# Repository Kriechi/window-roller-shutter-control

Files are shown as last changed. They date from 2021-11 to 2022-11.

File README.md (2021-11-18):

# Window Roller Shutter Control 3-gang with ESP8266

This project contains a 3-gang electric/motorized window roller shutter control
based on an ESP8266. The following resources are included:

* Full schematics and PCB designs
  * in KiCAD 5 with all footprints
  * generated Gerber files ready to send to PCB manufacturer
  * exported as PDF file
* Microcontroller ESP8266 firmware source code
  * with WiFi connectivity and remote over-the-air update
  * for control via MQTT and a web interface
* 3D-printable enclosure
  * in 3MF and STL file formats

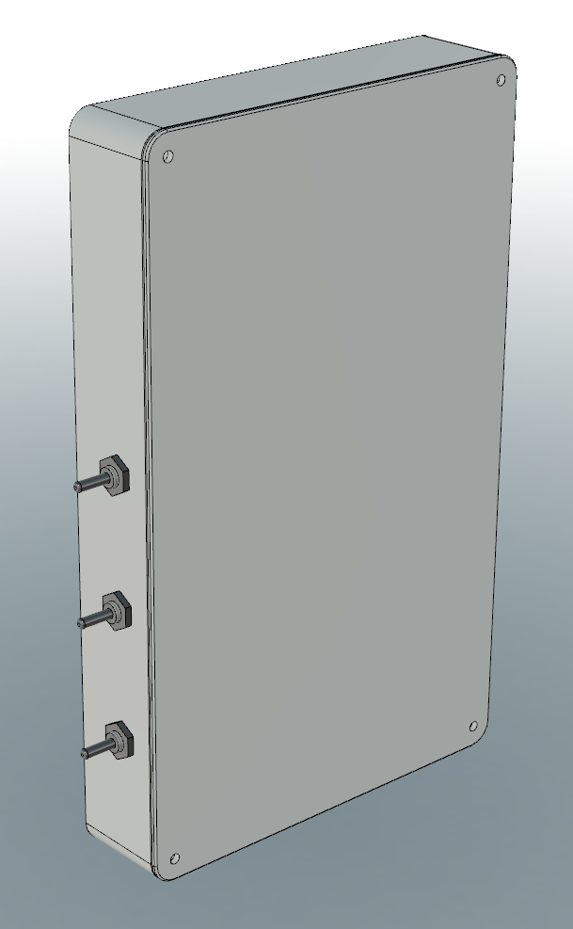
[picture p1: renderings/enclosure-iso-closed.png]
enclosure-iso-closed


## Hardware

This projects was designed to control 3 independent electric roller shutter
motors, each with a hot (live) and two switched directional wires (L1 for "up"
and L2 for "down"). Existing manual switches need to be removed and the motor
cables are wired to screw terminals on the PCB. Two relays per roller shutter
control the direction: up or down. The circuit and the relay type ensure that
only one direction is possible at a time. The relays open before closing
(break-before-make), and both relays are arranged "in series" to control the
motor direction.

The PCB and enclosure are designed to fit around an existing 3-gang 60mm switch
box. Any common 3-gang switch plate for this size can be replaced by the PCB and
enclosure, given that each switch box is 72mm apart from its neighbor switch
box. The enclosure mounts flush against the wall and is secured by multiple
screws into the switch box behind it.

Since not every roller shutter provides a neutral (return) wire, an external
5-24VDC power supply (wall plug) is used to power the ESP8266 and relays on PCB.
This securely separates low-voltage from high-voltage, also see separation slots
on the PCB. Multiple footprints are on the PCB to feed in DC low-voltage.

Momentary toggle switches can be added to manually control the roller shutters,
independent of the ESP8266 or automation. The enclosure is designed for 6mm
toggle switches. They control the relays low-voltage side and override signals
from the ESP8266.

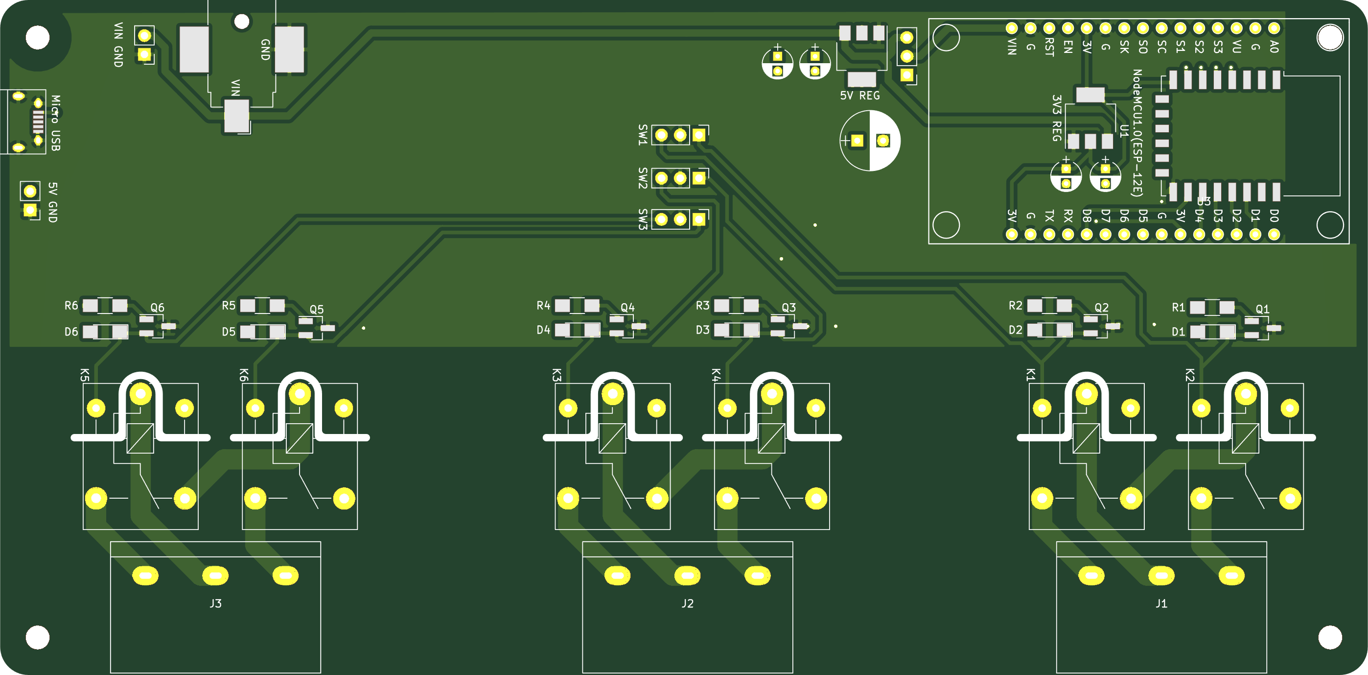
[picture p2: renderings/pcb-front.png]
pcb-front

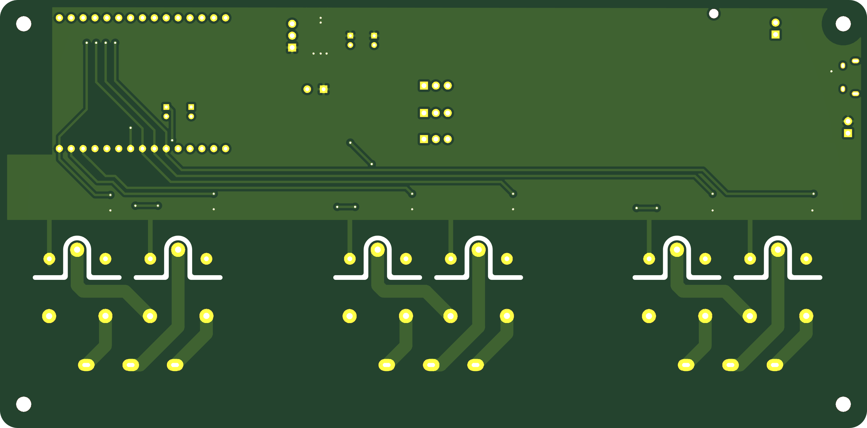
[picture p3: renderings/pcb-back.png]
pcb-back


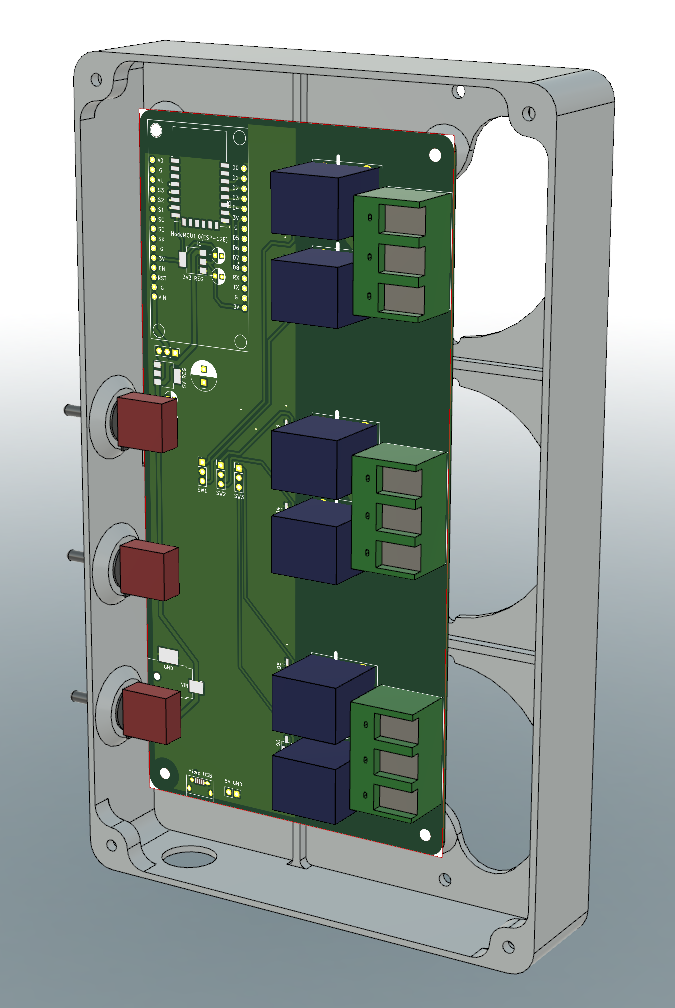
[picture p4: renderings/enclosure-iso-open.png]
enclosure-iso-open


### Bill of Material

For the PCB assembly:

* 1x NodeMCU module for ESP8266, or ESP-12E module (requires additional components)
* 3x HB-9500 3P screw terminal, 9.5mm pitch
* 6x SRD-05VDC-SL-C relay, 5VDC control, opening before closing, 10A@250VAC
* 6x NPN transistor, footprint SOT-23, 2N3904 or similar
* 6x 220 Ohm resistor, footprint 1206
* 6x flyback diode, footprint 1206, 1N4001 or similar
* 3x MTS-123 On-Off-On toggle switch
* 1x 5V DC-DC voltage regulator, footprint SOT-223-3, AMS1117-50 or similar
* 1x 3.3V DC-DC voltage regulator if ESP-12E is used, footprint SOT-223-3, AMS1117-33 or similar
* 1x suitable power supply for 5VDC, at least 10W
* optional: capacitors as needed per voltage rail

For the enclosure and mounting:

* 8x M3 nut
* 4x M3x12 bolts
* 2x 3.2mm switch box screws (optional, up to 6x)

### Wiring

Each roller shutter is controlled by two relays accessible via a 3-way screw
terminal block. The center connection is the hot / live wire. The outer
connections are the directional L1 and L2 wires. If you roller shutters is
moving in the wrong direction, e.g., up instead of down, simply reverse the
wires on the outer connections on the this screw terminal block.

The toggle switches are wired in a similar way: the center pin is the common
connection, and the two outer pins control the up or down signal to the ESP8266.

The ESP8266 ESP-12E module needs an external 3.3V regulator, while the NodeMCU
module has one built in and only needs a 5V input (see available footprints on
the PCB). Various footprints for decoupling capacitors are available and can be
populated.

## Firmware / Control Software

The ESP8266 microcontroller can be flashed with the provided PlatformIO-based
firmware project. It controls the following functions:

* WiFi connectivity
* MQTT connection
  * with status updates being published to `window_shutter_status` topic
  * with action commands being subscribed to on the `window_shutter` topic
* Web interface
  * to invoke commands via a browser-based UI
  * similar actions as via MQTT
* Over-the-air updates

All credentials and configuration is placed in `include/credentials.h`, see the
included template file for structure and variable names: WiFi SSID and
passphrase; MQTT server, username and password; and optional an OTA password.

After power-up and connecting to a WiFi network, the web-based UI is available
on the assigned IP address via HTTP (port 80). It is a simple frontend for the
following HTTP calls:

* `/action?q=...` with `...` being an action or preset
  * `1u` or `1up` to move the first shutter up
  * `1d` or `1down` to move the first shutter down
  * `2u` or `2up` to move the second shutter up
  * `2d` or `2down` to move the second shutter down
  * `3u` or `3up` to move the third shutter up
  * `3d` or `3down` to move the third shutter down
  * `preset_work`, `preset_normal`, `preset_night` activates one of the hardcoded presets
  * `s` or `stop` is the same as `/stop`
* `/stop` to stop all roller shutters by disabling the relays
* `/restart` to restart the ESP8266 microcontroller

Similar to the web UI, an MQTT connection is established after power-up and two
topics are use:

* status updates are published to `window_shutter_status`
  * contains state change messages and debug information
* commands can be published to `window_shutter` for the ESP8266 to act upon with a payload
  * `1u` or `1up` to move the first shutter up
  * `1d` or `1down` to move the first shutter down
  * `2u` or `2up` to move the second shutter up
  * `2d` or `2down` to move the second shutter down
  * `3u` or `3up` to move the third shutter up
  * `3d` or `3down` to move the third shutter down
  * `preset_work`, `preset_normal`, `preset_night` activates one of the hardcoded presets
  * `s` or `stop` to stop all roller shutters by disabling the relays
  * `restart` to restart the ESP8266 microcontroller

See [PlatformIO](https://platformio.org/) for more information on how to get
started, compile, and upload the firmware.

Quick development commands:

* compile and verify the code: `platformio run`
* compile and upload the code: `platformio run --target upload`
* get a serial console of the device: `platformio device monitor`

## Caveats

During power-up of the ESP8266, some pins might change state and trigger a relay
to close, before the firmware sets the correct state. This momentary change can
activate the roller shutter for a fraction of a second but is not happening
during normal operation.

If the used power supply is not capable of providing enough switching current
when the relays activate, you can bump up the input voltage to 7.5 or 9VDC, or
add more capacitance on the regulated 5VDC rail.

The toggle switches directly activate the relay, bypassing the
ESP8266-controlled transistors. However, due to the "in series" arrangement of
both relays, if the ESP8266 sends a "down" signal, a toggle switch might not be
able to override it in one direction.

When using an ESP-12E module, extra pull-up or pull-down resistors might be
needed (no footprints on the PCB). The NodeMCU module can be inserted into
standard 2.54mm headers and works with only a 5VDC input voltage.

## License

This project is made available under the MIT License. For more details, see the
``LICENSE`` file in the repository.

## Author

This project was created by Thomas Kriechbaumer.

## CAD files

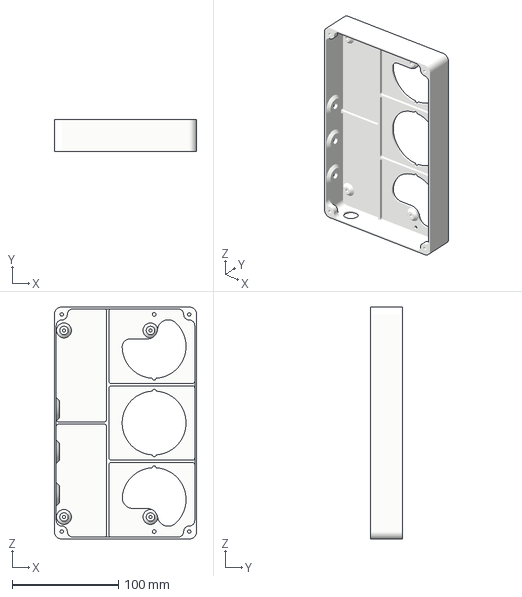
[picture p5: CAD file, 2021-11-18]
enclosure/main-housing.3mf
133.8 x 29.9 x 218.0 mm

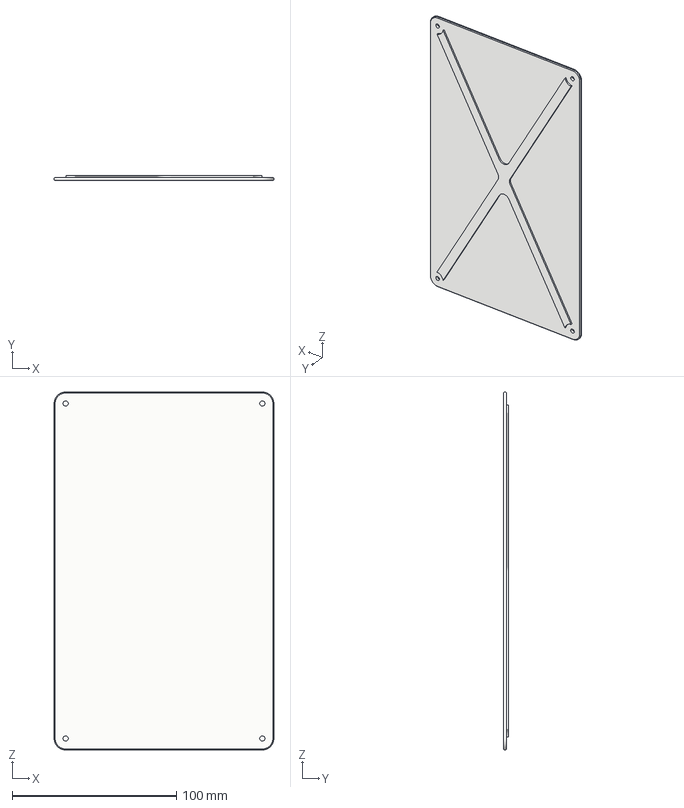
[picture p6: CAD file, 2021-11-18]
enclosure/lid.3mf
133.8 x 3.30 x 218.0 mm

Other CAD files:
enclosure/lid.stl
enclosure/main-housing.stl

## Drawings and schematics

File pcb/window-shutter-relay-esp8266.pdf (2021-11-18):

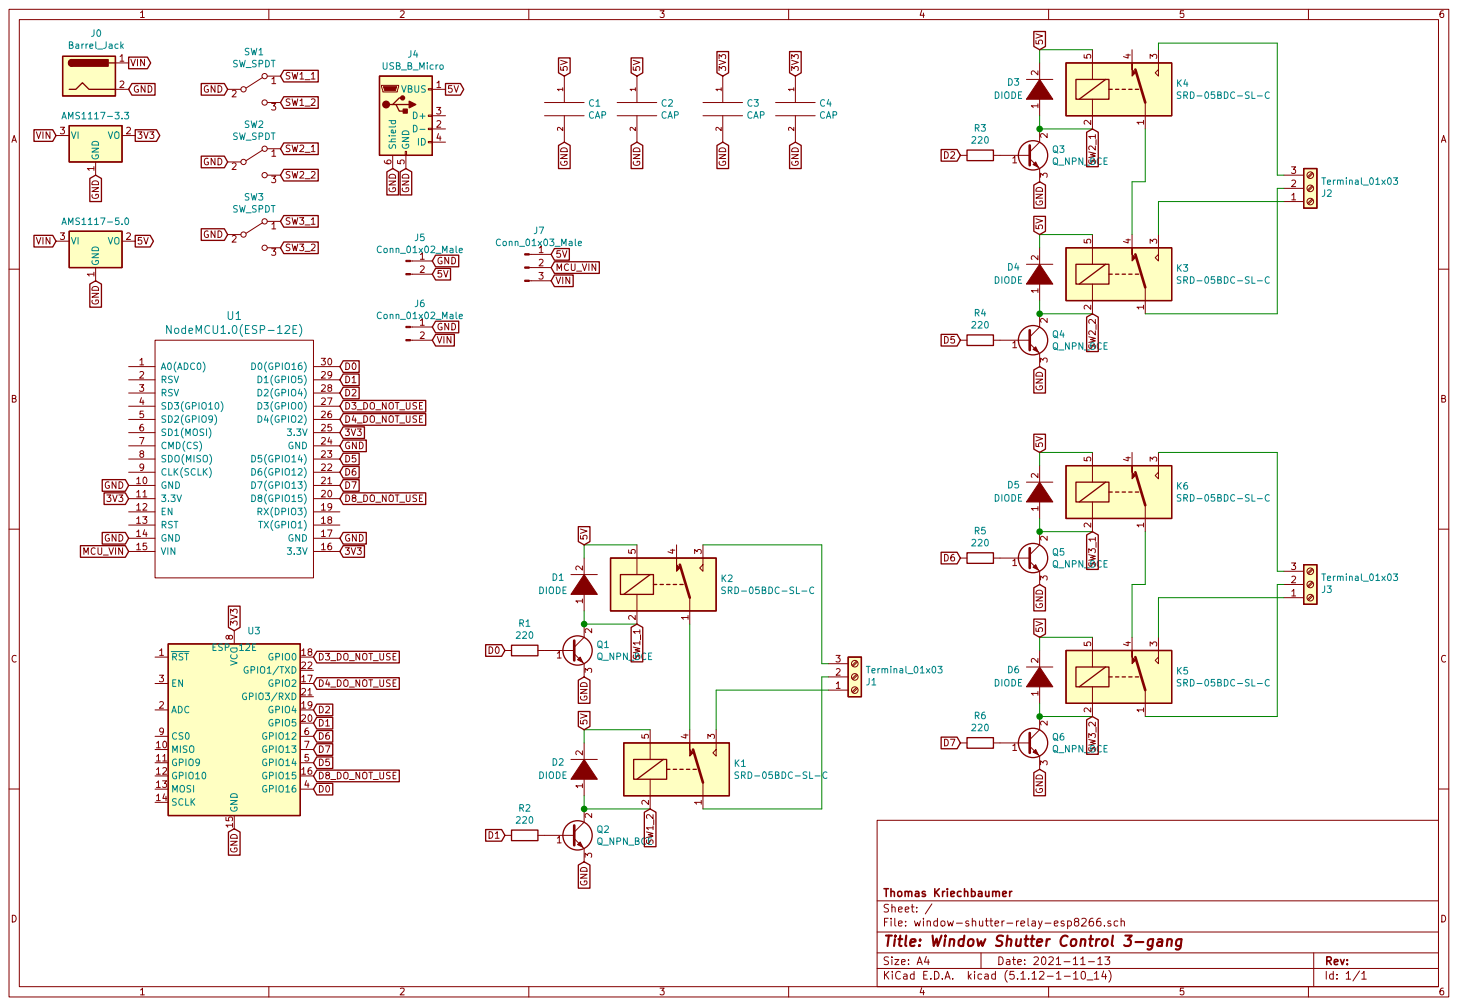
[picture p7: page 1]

1 2 D6 DIODE RST 1 MISO 10 GPIO9 11 GPIO10 12 MOSI 13 SCLK 14 GND 15 GPIO15 16 GPIO2 17 GPIO0 18 GPIO4 19 ADC 2 GPIO5 20 GPIO3/RXD 21 GPIO1/TXD 22 EN 3 GPIO16 4 GPIO14 5 GPIO12 6 GPIO13 7 VCC

Id: 1/1 Title: Window Shutter Control 3-gang

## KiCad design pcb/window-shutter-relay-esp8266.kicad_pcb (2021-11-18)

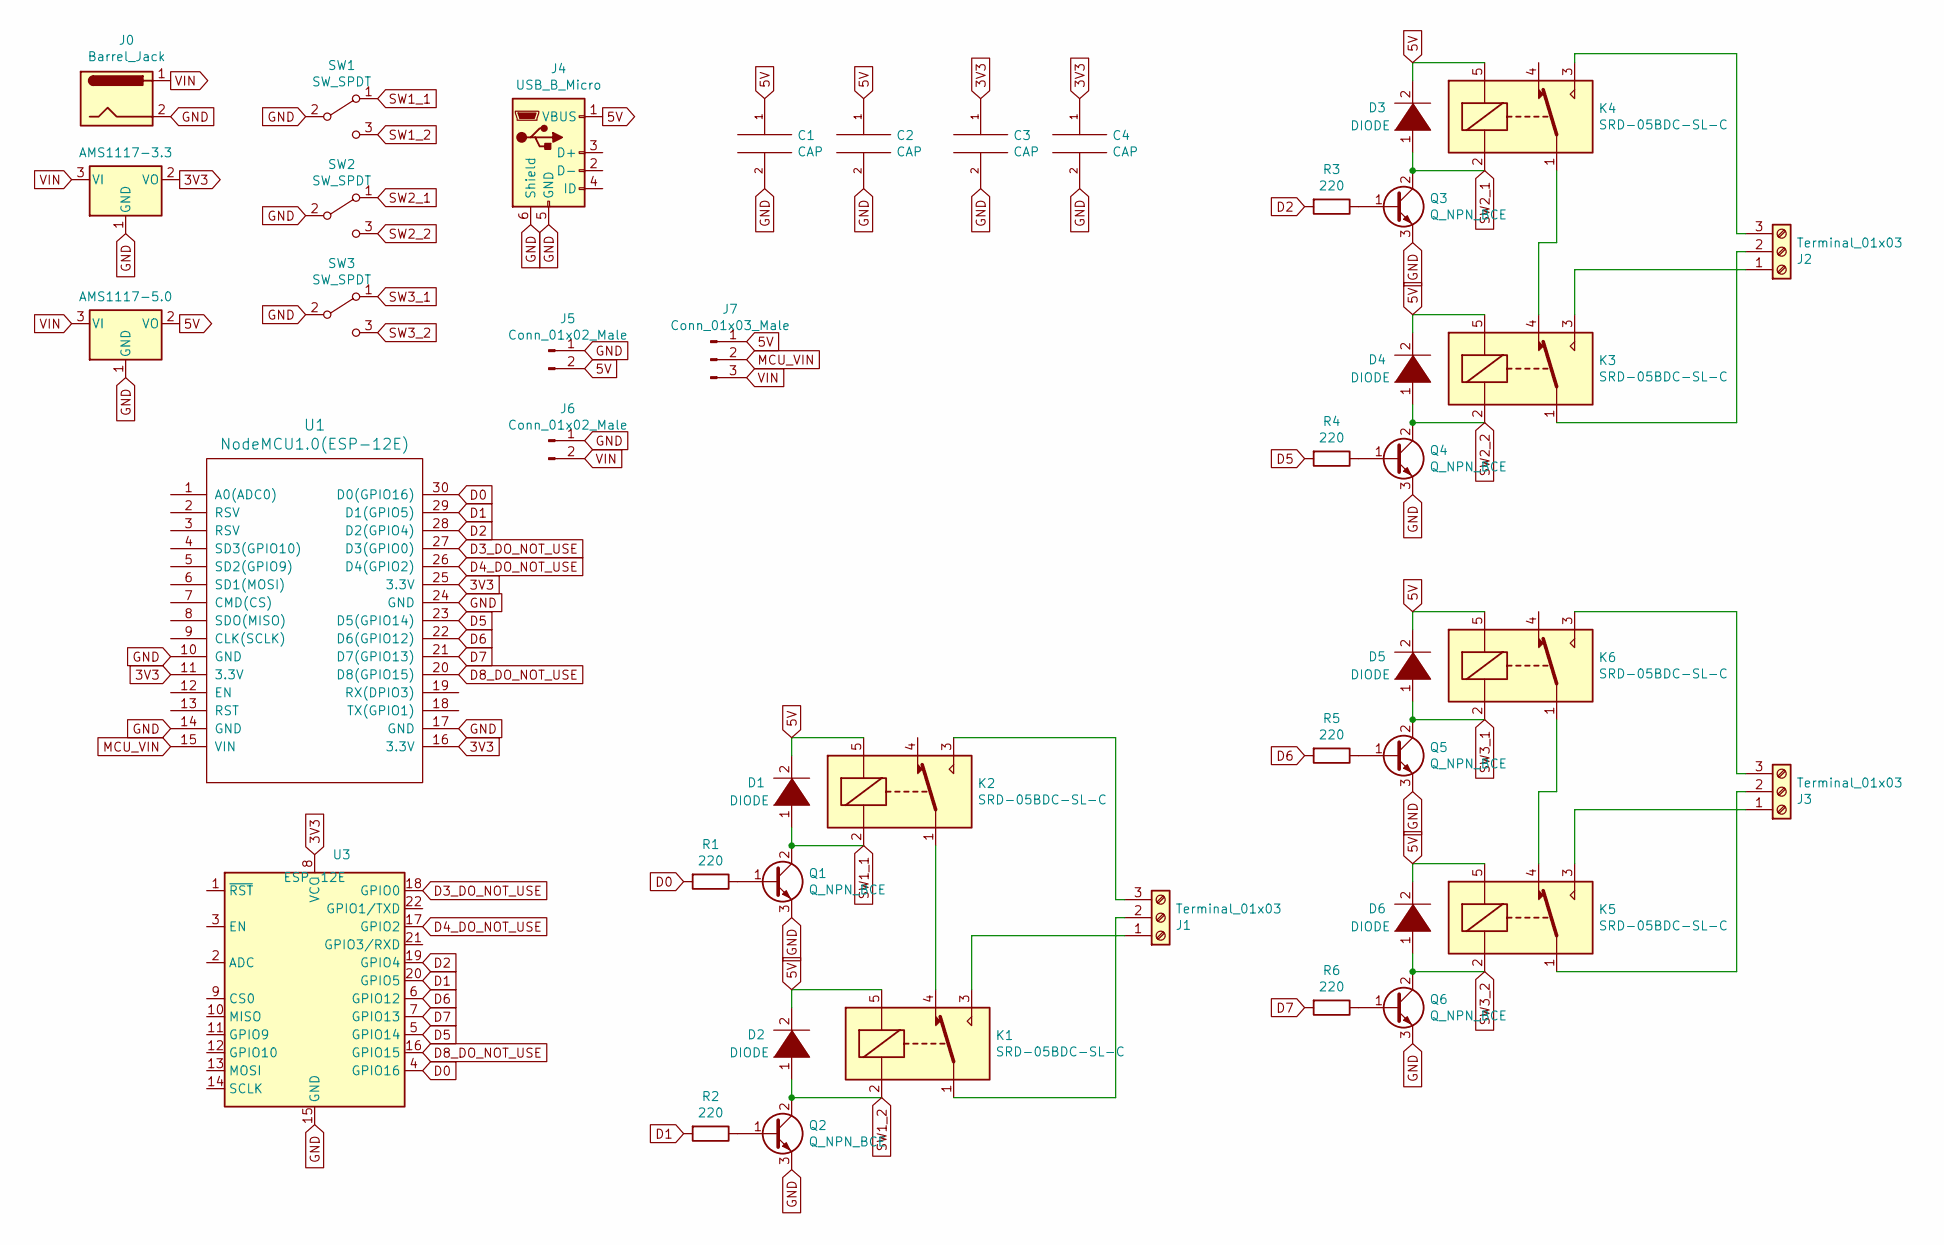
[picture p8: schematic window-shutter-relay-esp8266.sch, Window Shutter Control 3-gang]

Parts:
C1, C2, C3, C4: CAP; CP_Radial_D4.0mm_P2.00mm
D1, D2, D3, D4, D5, D6: DIODE; LED_1206_HandSoldering
J0: Barrel_Jack; Barrel_Jack_CUI_PJ-036AH-SMT
J1, J2, J3: Terminal_01x03; TerminalBlock_HB-9500-3_P9.50mm
J4: USB_B_Micro; USB_Micro-B
J5, J6: Conn_01x02_Male; Pin_Header_Straight_1x02_Pitch2.54mm
J7: Conn_01x03_Male; Pin_Header_Straight_1x03_Pitch2.54mm
K1, K2, K3, K4, K5, K6: SRD-05BDC-SL-C; Relay_SPDT_SANYOU_SRD_Series_Form_C
Q1, Q2, Q3, Q4, Q5, Q6: Q_NPN_BCE; SOT-23_Handsoldering
R1, R2, R3, R4, R5, R6: 220; R_1206_HandSoldering
SW1, SW2, SW3: SW_SPDT; Pin_Header_Straight_1x03_Pitch2.54mm
U1: NodeMCU1.0(ESP-12E); NodeMCU-LoLinV3
U2: AMS1117-5.0; SOT-223-3_TabPin2
U3: ESP-12E; ESP-12E_SMD
U4: AMS1117-3.3; SOT-223-3_TabPin2

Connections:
3V3: C3.1, C4.1, U1.11 (3.3V), U1.16 (3.3V), U1.25 (3.3V), U3.8 (VCC), U4.2 (VO)
5V: C1.1, C2.1, D1.2 (A), D2.2 (A), D3.2 (A), D4.2 (A), D5.2 (A), D6.2 (A), J4.1 (VBUS), J5.2, J7.1, K1.5, K2.5, K3.5, K4.5, K5.5, K6.5, U2.2 (VO)
D0: R1.2, U1.30 (D0(GPIO16)), U3.4 (GPIO16)
D1: R2.2, U1.29 (D1(GPIO5)), U3.20 (GPIO5)
D2: R3.2, U1.28 (D2(GPIO4)), U3.19 (GPIO4)
D3_DO_NOT_USE: U1.27 (D3(GPIO0)), U3.18 (GPIO0)
D4_DO_NOT_USE: U1.26 (D4(GPIO2)), U3.17 (GPIO2)
D5: R4.2, U1.23 (D5(GPIO14)), U3.5 (GPIO14)
D6: R5.2, U1.22 (D6(GPIO12)), U3.6 (GPIO12)
D7: R6.2, U1.21 (D7(GPIO13)), U3.7 (GPIO13)
D8_DO_NOT_USE: U1.20 (D8(GPIO15)), U3.16 (GPIO15)
GND: C1.2, C2.2, C3.2, C4.2, J0.2, J4.5 (GND), J4.6 (Shield), J5.1, J6.1, Q1.3 (E), Q2.3 (E), Q3.3 (E), Q4.3 (E), Q5.3 (E), Q6.3 (E), SW1.2 (B), SW2.2 (B), SW3.2 (B), U1.10 (GND), U1.14 (GND), U1.17 (GND), U1.24 (GND), U2.1 (GND), U3.15 (GND), U4.1 (GND)
MCU_VIN: J7.2, U1.15 (VIN)
unnamed: J1.1, K1.3
unnamed: J1.2, K1.1
unnamed: J1.3, K2.3
unnamed: J2.1, K3.3
unnamed: J2.2, K3.1
unnamed: J2.3, K4.3
unnamed: J3.1, K5.3
unnamed: J3.2, K5.1
unnamed: J3.3, K6.3
unnamed: K1.4, K2.1
unnamed: K3.4, K4.1
unnamed: K5.4, K6.1
unnamed: Q1.1 (B), R1.1
unnamed: Q2.1 (B), R2.1
unnamed: Q3.1 (B), R3.1
unnamed: Q4.1 (B), R4.1
unnamed: Q5.1 (B), R5.1
unnamed: Q6.1 (B), R6.1
SW1_1: D1.1 (K), K2.2, Q1.2 (C), SW1.1 (A)
SW1_2: D2.1 (K), K1.2, Q2.2 (C), SW1.3 (C)
SW2_1: D3.1 (K), K4.2, Q3.2 (C), SW2.1 (A)
SW2_2: D4.1 (K), K3.2, Q4.2 (C), SW2.3 (C)
SW3_1: D5.1 (K), K6.2, Q5.2 (C), SW3.1 (A)
SW3_2: D6.1 (K), K5.2, Q6.2 (C), SW3.3 (C)
VIN: J0.1, J6.2, J7.3, U2.3 (VI), U4.3 (VI)

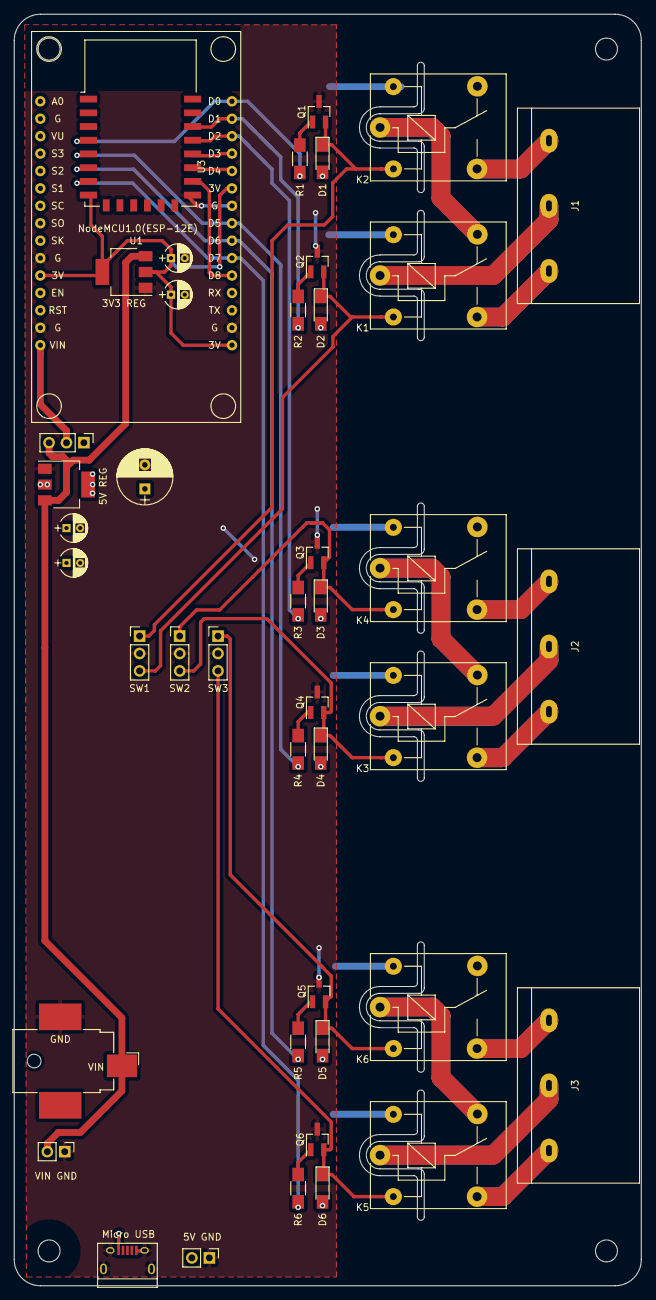
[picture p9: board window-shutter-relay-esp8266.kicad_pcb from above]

Board: 2 copper layers, 91.4 x 185.4 mm, 43 parts (0 on the bottom side), 38 nets.

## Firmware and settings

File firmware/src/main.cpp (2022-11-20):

#include <ESP8266WiFi.h>
#include <ESP8266WebServer.h>
#include <NTPClient.h>
#include <PubSubClient.h>
#include <ArduinoOTA.h>
#include <Ticker.h>

#include "credentials.h"

const int WINDOW_1_A = D1;
const int WINDOW_1_B = D0;
const int WINDOW_2_A = D7;
const int WINDOW_2_B = D2;
const int WINDOW_3_A = D5;
const int WINDOW_3_B = D6;

// B=LOW, A=HIGH => window shutter going up
// A=LOW, B=HIGH => window shutter going down

float DEFAULT_POSITION_TIME = 30.0;

#include "cert.h"
X509List cert(cert_ISRG_Root_X1);

WiFiUDP ntpUDP;
NTPClient timeClient(ntpUDP);

WiFiClientSecure wifi_client;
PubSubClient mqtt_client(wifi_client);
unsigned int mqtt_reconnect_counter = 0;

ESP8266WebServer server(80);

Ticker deenergize_ticker[6];

bool presets_mqtt_enabled = true;

void setup_wifi();
void setup_relays();
void setup_webserver();
void setup_ota();
void handleHTTPRoot();
void handleHTTPAction();
void handleHTTPStop();
void handleHTTPEnable();
void handleHTTPDisable();
void handleHTTPRestart();
void mqttCallback(char *topic, byte *payload, unsigned int length);
void reconnect();
void action(char window, char direction);
void action(char window, char direction, float position);
void toggle_shutter(int inactive, int active);
void toggle_shutter(int inactive, int active, float position);
void deenergize(int active);
void preset_work_day();
void preset_normal_day();
void preset_night();

unsigned int translate_pin(unsigned int pin)
{
  switch (pin)
  {
  case WINDOW_1_A:
    return 0;
  case WINDOW_1_B:
    return 1;
  case WINDOW_2_A:
    return 2;
  case WINDOW_2_B:
    return 3;
  case WINDOW_3_A:
    return 4;
  case WINDOW_3_B:
    return 5;
  default:
    return UINT32_MAX;
  }
}

void setup()
{
  Serial.begin(115200);
  Serial.println();
  Serial.println();

  setup_wifi();

  randomSeed(micros());

  setup_relays();

  wifi_client.setTrustAnchors(&cert);
  wifi_client.setInsecure();
  mqtt_client.setServer(mqtt_server, mqtt_port);
  mqtt_client.setCallback(mqttCallback);
  mqtt_reconnect_counter = 0;

  setup_webserver();
  setup_ota();

  Serial.println("Setup complete.");
}

void setup_wifi()
{
  Serial.print("Connecting to ");
  Serial.println(ssid);

  WiFi.mode(WIFI_STA);
  WiFi.begin(ssid, wifi_password);

  while (WiFi.status() != WL_CONNECTED)
  {
    delay(500);
    Serial.print(".");
  }

  Serial.println("");
  Serial.println("WiFi connected");
  Serial.print("IP address: ");
  Serial.println(WiFi.localIP());

  timeClient.begin();
  timeClient.forceUpdate();
  delay(1000);
  Serial.printf("NTP updated: %lu\n", timeClient.getEpochTime());
}

void setup_relays()
{
  pinMode(WINDOW_1_B, OUTPUT);
  digitalWrite(WINDOW_1_B, LOW);
  pinMode(WINDOW_1_A, OUTPUT);
  digitalWrite(WINDOW_1_A, LOW);
  pinMode(WINDOW_2_B, OUTPUT);
  digitalWrite(WINDOW_2_B, LOW);
  pinMode(WINDOW_2_A, OUTPUT);
  digitalWrite(WINDOW_2_A, LOW);
  pinMode(WINDOW_3_B, OUTPUT);
  digitalWrite(WINDOW_3_B, LOW);
  pinMode(WINDOW_3_A, OUTPUT);
  digitalWrite(WINDOW_3_A, LOW);
}

void setup_webserver()
{
  server.on("/", handleHTTPRoot);
  server.on("/action", handleHTTPAction);
  server.on("/stop", handleHTTPStop);
  server.on("/enable", handleHTTPEnable);
  server.on("/disable", handleHTTPDisable);
  server.on("/restart", handleHTTPRestart);
  server.begin();
  Serial.println("HTTP server started");
}

void setup_ota()
{
  // ArduinoOTA.setPassword(ota_password);
  ArduinoOTA.onStart([]()
                     {
                       String type;
                       if (ArduinoOTA.getCommand() == U_FLASH)
                       {
                         type = "sketch";
                       }
                       else
                       { // U_FS
                         type = "filesystem";
                       }
                       // NOTE: if updating FS this would be the place to unmount FS using FS.end()
                       Serial.println("Start updating " + type);
                     });
  ArduinoOTA.onEnd([]()
                   { Serial.println("\nEnd"); });
  ArduinoOTA.onProgress([](unsigned int progress, unsigned int total)
                        { Serial.printf("Progress: %u%%\r", (progress / (total / 100))); });
  ArduinoOTA.onError([](ota_error_t error)
                     {
                       Serial.printf("Error[%u]: ", error);
                       if (error == OTA_AUTH_ERROR)
                       {
                         Serial.println("Auth Failed");
                       }
                       else if (error == OTA_BEGIN_ERROR)
                       {
                         Serial.println("Begin Failed");
                       }
                       else if (error == OTA_CONNECT_ERROR)
                       {
                         Serial.println("Connect Failed");
                       }
                       else if (error == OTA_RECEIVE_ERROR)
                       {
                         Serial.println("Receive Failed");
                       }
                       else if (error == OTA_END_ERROR)
                       {
                         Serial.println("End Failed");
                       }
                     });
  ArduinoOTA.begin();
}

void loop()
{
  ArduinoOTA.handle();

  timeClient.update();

  server.handleClient();

  if (!mqtt_client.connected())
  {
    reconnect();
  }
  mqtt_client.loop();
}

void reconnect()
{
  if (WiFi.status() != WL_CONNECTED)
  {
    setup_wifi();
  }

  wifi_client.setX509Time(timeClient.getEpochTime());

  Serial.print("Attempting MQTT connection...");
  // Create a random client ID
  String clientId = "WindowShutter-";
  clientId += String(random(0xffff), HEX);
  // Attempt to connect
  if (mqtt_client.connect(clientId.c_str(), mqtt_username, mqtt_password))
  {
    mqtt_reconnect_counter += 1;
    Serial.println(" connected.");
    String msg = "Fiat Lux for the " + String(mqtt_reconnect_counter) + "th time! My IP is " + WiFi.localIP().toString() + " an I'm up for " + millis() + "millisec.";
    mqtt_client.publish("window_shutter_status", msg.c_str());
    mqtt_client.subscribe("window_shutter");
  }
  else
  {
    Serial.print("failed, rc=");
    Serial.print(mqtt_client.state());
    delay(1000);
  }
}

void action(char window, char direction)
{
  action(window, direction, DEFAULT_POSITION_TIME);
}

void action(char window, char direction, float position)
{
  if (window == '1' && direction == 'd')
  {
    Serial.println("Window 1 down...");
    mqtt_client.publish("window_shutter_status", "Window 1 down...");
    toggle_shutter(WINDOW_1_A, WINDOW_1_B, position);
  }
  else if (window == '1' && direction == 'u')
  {
    Serial.println("Window 1 up...");
    mqtt_client.publish("window_shutter_status", "Window 1 up...");
    toggle_shutter(WINDOW_1_B, WINDOW_1_A, position);
  }
  else if (window == '2' && direction == 'd')
  {
    Serial.println("Window 2 down...");
    mqtt_client.publish("window_shutter_status", "Window 2 down...");
    toggle_shutter(WINDOW_2_A, WINDOW_2_B, position);
  }
  else if (window == '2' && direction == 'u')
  {
    Serial.println("Window 2 up...");
    mqtt_client.publish("window_shutter_status", "Window 2 up...");
    toggle_shutter(WINDOW_2_B, WINDOW_2_A, position);
  }
  else if (window == '3' && direction == 'd')
  {
    Serial.println("Window 3 down...");
    mqtt_client.publish("window_shutter_status", "Window 3 down...");
    toggle_shutter(WINDOW_3_A, WINDOW_3_B, position);
  }
  else if (window == '3' && direction == 'u')
  {
    Serial.println("Window 3 up...");
    mqtt_client.publish("window_shutter_status", "Window 3 up...");
    toggle_shutter(WINDOW_3_B, WINDOW_3_A, position);
  }
}

void action_stop()
{
  digitalWrite(WINDOW_1_A, LOW);
  digitalWrite(WINDOW_1_B, LOW);
  digitalWrite(WINDOW_2_A, LOW);
  digitalWrite(WINDOW_2_B, LOW);
  digitalWrite(WINDOW_3_A, LOW);
  digitalWrite(WINDOW_3_B, LOW);

  for (auto &&t : deenergize_ticker)
  {
    t.detach();
  }

  mqtt_client.publish("window_shutter_status", "stopped");
}

void handleHTTPRoot()
{
  // minify index.html and replace in between rawliteral here
  String index_html = R"rawliteral(
      <!DOCTYPE html><html><head><meta charset="utf-8"><meta name="viewport" content="width=device-width,initial-scale=1,user-scalable=no"><meta name="apple-mobile-web-app-capable" content="yes"><title>Window Roller Shutters</title><style>body{text-align:center;font-family:sans-serif;background:#2c2c2c}#main{text-align:center;display:inline-block;color:#f0f0f0;min-width:340px}table{width:100%}a{color:#f0f0f0;text-decoration:none}button{border:0;border-radius:.5rem;background:#25abf3;color:#f0f0f0;line-height:3rem;font-size:1.3rem;width:100%}button:hover{background:#1377ad}</style></head><body><div id="main"><h2>Window Roller Shutters</h2><table><tr><td colspan="3"><button class="action" name="preset_work_day">Work Day</button></td></tr><tr><td colspan="3"><button class="action" name="preset_normal_day">Day</button></td></tr></table><hr><table><tr><td><button class="action" name="1u">1 Up</button></td><td><button class="action" name="2u">2 Up</button></td><td><button class="action" name="3u">3 Up</button></td></tr><tr><td><button class="action" name="1d">1 Down</button></td><td><button class="action" name="2d">2 Down</button></td><td><button class="action" name="3d">3 Down</button></td></tr></table><hr><table><tr><td colspan="3"><button class="action" name="preset_night">Night</button></td></tr></table><hr><table><tr><td><button class="action" name="stop">Stop</button></td></tr></table><hr><table><tr><td><a href="{{enable_action}}"><button>{{enable_state}}</button></a></td></tr></table><hr><p><a href="/restart">Restart</a></p><script>els = document.getElementsByClassName("action");Array.from(els).forEach((el) => {el.addEventListener("click", function (e) {var xhttp = new XMLHttpRequest();xhttp.open("GET", "/action?q=" + e.target.name, true);xhttp.send();});});</script></div></body></html>
    )rawliteral";

  index_html.replace("{{enable_state}}", presets_mqtt_enabled ? "Disable presets (currently enabled)" : "Enable presets (currently disabled)");
  index_html.replace("{{enable_action}}", presets_mqtt_enabled ? "disable" : "enable");

  server.send(200, "text/html", index_html);
}

void handleHTTPAction()
{
  if (server.hasArg("q") && server.arg("q").length() == 2 && (server.arg("q").charAt(0) == '1' || server.arg("q").charAt(0) == '2' || server.arg("q").charAt(0) == '3'))
  {
    action(server.arg("q").charAt(0), server.arg("q").charAt(1));
    server.send(200, "text/plain", "ok");
  }
  else if (server.hasArg("q") && server.arg("q") == "preset_work_day")
  {
    preset_work_day();
    server.send(200, "text/plain", "ok");
  }
  else if (server.hasArg("q") && server.arg("q") == "preset_normal_day")
  {
    preset_normal_day();
    server.send(200, "text/plain", "ok");
  }
  else if (server.hasArg("q") && server.arg("q") == "preset_night")
  {
    preset_night();
    server.send(200, "text/plain", "ok");
  }
  else if (server.hasArg("q") && (server.arg("q") == "s" || server.arg("q") == "stop"))
  {
    action_stop();
    server.send(200, "text/plain", "ok");
  }
  else
  {
    server.send(500, "text/plain", "error");
  }
}

void handleHTTPStop()
{
  action_stop();
  server.send(200, "text/plain", "ok");
}

void handleHTTPEnable()
{
  presets_mqtt_enabled = true;
  Serial.println("Enabled all actions.");
  handleHTTPRoot();
}

void handleHTTPDisable()
{
  presets_mqtt_enabled = false;
  Serial.println("Disabled all actions.");
  handleHTTPRoot();
}

void handleHTTPRestart()
{
  server.send(200, "text/plain", "ok");
  Serial.println("Restarting ESP...");
  ESP.restart();
}

void mqttCallback(char *t, byte *p, unsigned int length)
{
  String topic = String(t);
  String payload;
  for (size_t i = 0; i < length; i++)
  {
    payload.concat((char)p[i]);
  }

  if (topic != "window_shutter")
  {
    return;
  }

  String msg = payload + " " + payload.length();
  mqtt_client.publish("window_shutter_status", msg.c_str());

  if (payload == "restart")
  {
    Serial.println("Restarting ESP...");
    ESP.restart();
    return;
  }
  else if (payload == "s" || payload == "st" || payload == "sto" || payload == "stop")
  {
    Serial.println("Stopping all window shutters...");
    action_stop();
    return;
  }

  if (presets_mqtt_enabled && (payload == "preset_work_day" || payload == "work_day" || payload == "work" || payload == "w"))
  {
    preset_work_day();
  }
  else if (presets_mqtt_enabled && (payload == "preset_normal_day" || payload == "normal_day" || payload == "normal" || payload == "up" || payload == "u"))
  {
    preset_normal_day();
  }
  else if (presets_mqtt_enabled && (payload == "preset_night" || payload == "night" || payload == "down" || payload == "d"))
  {
    preset_night();
  }
  else if (payload.length() >= 2)
  {
    action((char)payload[0], (char)payload[1]);
  }
  else
  {
    Serial.println("WARN: unknown message!");
    Serial.println(payload);
  }
}

void toggle_shutter(int inactive, int active)
{
  toggle_shutter(inactive, active, DEFAULT_POSITION_TIME);
}

void toggle_shutter(int inactive, int active, float position)
{
  digitalWrite(inactive, LOW);
  deenergize_ticker[translate_pin(inactive)].detach();

  delay(250);

  digitalWrite(active, HIGH);
  deenergize_ticker[translate_pin(active)].once(position, deenergize, active);

  String msg = String("set relays ") + inactive + String("=OFF and ") + active + String("=ON");
  mqtt_client.publish("window_shutter_status", msg.c_str());
}

void deenergize(int active)
{
  digitalWrite(active, LOW);
  String msg = String("deenergized ") + active;
  mqtt_client.publish("window_shutter_status", msg.c_str());
}

void preset_work_day()
{
  mqtt_client.publish("window_shutter_status", "setting preset: work day...");
  action('1', 'u');
  action('2', 'u');
  action('3', 'u', 13.0);
}

void preset_normal_day()
{
  mqtt_client.publish("window_shutter_status", "setting preset: normal day...");
  action('1', 'u');
  action('2', 'u');
  action('3', 'u');
}

void preset_night()
{
  mqtt_client.publish("window_shutter_status", "setting preset: night...");
  action('1', 'd');
  action('2', 'd');
  action('3', 'd');
}

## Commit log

2022-01-29 add global disable/enable switch for all shutter actions
2022-11-20 KiCAD upgrade
